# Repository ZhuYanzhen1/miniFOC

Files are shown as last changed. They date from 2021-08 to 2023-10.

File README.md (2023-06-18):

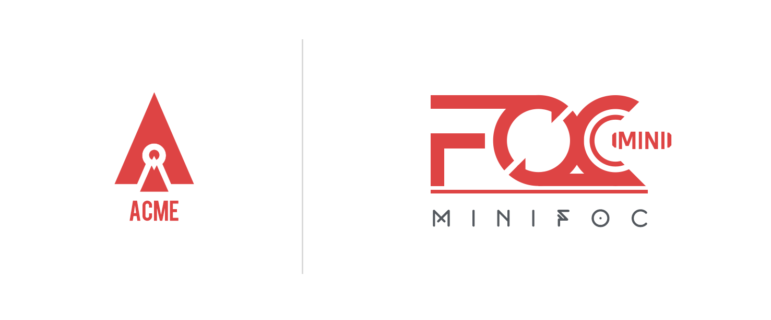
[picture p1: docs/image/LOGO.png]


&nbsp;&nbsp;&nbsp;&nbsp;&nbsp;&nbsp;&nbsp;&nbsp;&nbsp;&nbsp;&nbsp;&nbsp;&nbsp;&nbsp;&nbsp;&nbsp;English / [中文](https://github.com/ZhuYanzhen1/miniFOC/blob/main/README_CN.md)

&nbsp;&nbsp;&nbsp;&nbsp;Are you still buying a DC brush motor drive module in about 3<span>$</span>? Are you still worried about the high noise in addition to the already low response speed and life? Allow me to present you our project, miniFOC---- a FOC brushless motor control scheme that can get you the most bang for your buck, for just 3 <span>$</span>!  **miniFOC** has a built-in torque closed-loop controller so that you can control a brushless motor with a 3-wire UART port. The software and hardware design are fully compliant with the AGPL-3.0 open source license.

**Note: miniFOC V2 version is under development(dev branch) to support current loop and sensorless FOC algorithm, please look forward to it.**

***

### Brief Introduction

&nbsp;&nbsp;&nbsp;&nbsp;This open-source project aims to accomplish a FOC(Field Oriented Control) scheme that is operatable with minimum costs in China. The components selected in the example circuit are all manufactured in China. FOC possesses various advantages when it comes to controlling BLCD (Brushless Direct Current) motor; some of the benefits are as follows:

1. FOC has no speed limit at all and can be accurately controlled at any speed
2. FOC excels at its reversing performance, ensuring the smoothness of forward and reverse switching even when running at its highest speed
3. FOC can also perform braking control in the form of energy recovery.
4. FOC can achieve three closed-loop control of torque, speed, and position.
5. FOC has significantly lower noise but much higher efficiency compared that of electric regulation

&nbsp;&nbsp;&nbsp;Although FOC has many advantages, its large amount of calculation and complex principles requires an expensive controller, which made FOC unpopular. After half a year’s research and iteration, I deeply optimized the part of the code that implements mass calculations and re-selected its components to fit the domestic supply chain. I hope this open-source project can help domestic developers use BLDC motors with excellent performance and contribute to the open-source community.

***

### Comparison Of Open Source Solutions

| Open source solution | **miniFOC** | [simpleFOC](https://github.com/simplefoc/Arduino-SimpleFOCShield) | [ODrive](https://github.com/odriverobotics/ODrive) | [FpOC](https://github.com/WangXuan95/FpOC) |
| :---: | :---: | :---: | :---: | :---: |
| Microcontroller | GD32F130G6U6 | ATmega328P | STM32F405RGT6 | FPGA |
| Driver chip | EG2133 | L6234 | DRV8301 | MP6540 |
| PID loop frequency | 30kHz (max) | 830Hz (max) | 8kHz (typical) | 18kHz (typical) |
| Whether have current loop | No | No | Yes | Yes |
| Driving power | 90W | 120W | 960W | 90W |
| Cost price (approx.) | 20¥ | 100¥ | 300¥ | 150¥ |

&nbsp;&nbsp;&nbsp;&nbsp;As can be seen from the table above, the scheme adopted by **miniFOC** can achieve high performance at low cost. At the same time, due to the re-selection according to the domestic supply chain, the selection of devices is not so limited, and there are many alternatives. amid the chip shortage in 2021, the cost of FOC still can be controlled at about 3$, which further proves the degree of cost optimization and the great potential of the project.

***

### Performance Parameter 

+ Input voltage range: 5V ~ 18V (you can modify the circuit according to the tutorial here to adapt to higher voltage).
+ Maximum driving current: 5A (you can modify the circuit according to the tutorial here to achieve greater driving current).
+ Detailed parameters of FOC: no current loop control, SVPWM (Space Vector Pulse Width Modulation) is adopted.
+ Communication parameters: UART baud rate is 115200, and [Mid Capacity Data Transmit Protocol](https://github.com/ZhuYanzhen1/CDTP/blob/master/mdtp/README.md) is used for data transmission.
+ Microcontroller parameters: Cortex-M3 core, 72MHz frequency, 32KB FLASH, 4KB SRAM. 

***

### Function Features

+ [x] Using space vector pulse width modulation
+ [x] Torque control without current sensor
+ [x] Rotational speed closed loop control
+ [x] Rotation angle closed loop control
+ [x] Automatic phase sequence detection and correction

***

### Development Environment 

+ EDA Tool: [EasyEDA](https://easyeda.com/) (the standard free license is adopted, and there is no license dispute).
+ Compiler tool chain: gcc-arm-none-eabi 10-2020-q4-major
+ Programming tool: OpenOCD 0.11.0-1
+ Integrated development tools: CLion 2021.2.3 #212.5457.51
+ Software development tools: Qt 5.14.2 (MinGW 7.3.0 64bit)
+ Operating system and tool chain: 
  + Win10 + MinGW + CLion + gcc-arm-none-eabi + OpenOCD
  + Ubuntu20.04 + make + cmake + gcc-arm-none-eabi + OpenOCD

***

### Getting Started

Please refer to the [wiki page](https://github.com/ZhuYanzhen1/miniFOC/wiki) of this project for getting started.
<br>
We also provide the [domestic image](https://gitee.com/zhuyanzhen1/mini-foc) address.
<br>
You can visit [Github Page](https://zhuyanzhen1.github.io/miniFOC/) to learn about the usage of functions and variables in the code.
<br>
**Note:** Since the main development and deployment are carried out on Github, Gitee is only used as a domestic mirror warehouse to store the code, and there will be problems such as wiki and issue that are not updated in time. You can visit the Github source repository [here](https://github.com/ZhuYanzhen1/miniFOC).

***

### Bugs & Feature Requests

Please report bugs and request features using the [Issue Tracker](https://github.com/ZhuYanzhen1/miniFOC/issues) and follow these request:

1. Tab highlight when on different tab.
2. Don’t let the update disappear if the window is not in focus.

***

### License

The source code is released under a [AGPL-3.0 License](https://github.com/ZhuYanzhen1/miniFOC/blob/main/LICENSE).

**Affiliation：AcmeTech<br>
Author: Zhu Yanzhen<br>
Maintainer：YanzhenZhu, 2208213223@qq.com**

&nbsp;&nbsp;&nbsp;&nbsp;The product has been tested under Windows 10 and Ubuntu 18.04 and 20.04. This is research code, expect that it changes often and any fitness for a particular purpose is disclaimed.

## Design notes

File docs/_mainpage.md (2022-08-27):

### Function manual / 函数手册
### Introduction / 简介

&nbsp;&nbsp;&nbsp;&nbsp;This GitHub page is automatically generated by Doxygen according to code comments. It describes the purpose, function and usage of functions, variables and structures in each file except the library functions provided by gd32. You can click the "file - > file list" button at the top of the page to jump to the file list to view the description of the variables and functions declared in the relevant files.

&nbsp;&nbsp;&nbsp;&nbsp;本Github Page由Doxygen根据代码注释自动生成，描述了除了GD32提供的库函数外的每个文件中函数、变量与结构体的用途、功能和用法。你可以通过点击页面上方的“File -> File List”按钮跳转到文件列表以查看相关文件内部声明的变量和函数的说明。

### Download and  Description / 下载与描述

&nbsp;&nbsp;&nbsp;&nbsp;The content published below is the. Hex firmware generated by GitHub action scheduled task every time. The purpose is to automatically compile and publish the latest committed firmware under the main branch without manual compilation by the developer. It should be noted that the. Hex firmware on this page does not guarantee its stability and availability. If you want to download stable and available firmware, please go to the [Release Page](https://github.com/ZhuYanzhen1/miniFOC/releases) to download it.

&nbsp;&nbsp;&nbsp;&nbsp;下面发布的内容是每次由Github Action定时任务生成的.hex固件，目的是自动编译发布main分支下最新commit的固件而无需开发者手动编译。需要注意的是，本页面下的.hex固件不保证它的稳定性和可用性。如果你想下载稳定可用的固件，请转到[Release页面](https://github.com/ZhuYanzhen1/miniFOC/releases)下载。&nbsp;
 
+ [20220827](https://raw.githubusercontent.com/ZhuYanzhen1/miniFOC_Firmware/master/202208/20220827.hex): 5edd0af Merge branch 'main' of github.com:ZhuYanzhen1/miniFOC
 
+ [20220802](https://raw.githubusercontent.com/ZhuYanzhen1/miniFOC_Firmware/master/202208/20220802.hex): 6951035 Update Doxygen documentation

+ [20220801](https://raw.githubusercontent.com/ZhuYanzhen1/miniFOC_Firmware/master/202208/20220801.hex): abed215 Add SVPWM modulation code, which can be controlled by using macros.

+ [20220524](https://raw.githubusercontent.com/ZhuYanzhen1/miniFOC_Firmware/master/202205/20220524.hex): dd0dbc8 Update cmake.yml

+ [20211108](https://raw.githubusercontent.com/ZhuYanzhen1/miniFOC_Firmware/master/202111/20211108.hex): df8533c Change the automatic compilation workflow to run only when the push event occurs.

+ [20211107](https://raw.githubusercontent.com/ZhuYanzhen1/miniFOC_Firmware/master/202111/20211107.hex): bb8409a Update new firmware link to Github Pages

+ [20211106](https://raw.githubusercontent.com/ZhuYanzhen1/miniFOC_Firmware/master/202111/20211106.hex): 62c17af Merge branch 'main' of github.com:ZhuYanzhen1/miniFOC into main

+ [20211105](https://raw.githubusercontent.com/ZhuYanzhen1/miniFOC_Firmware/master/202111/20211105.hex): 08164bb Merge remote-tracking branch 'origin/main' into main

+ [20211104](https://raw.githubusercontent.com/ZhuYanzhen1/miniFOC_Firmware/master/202111/20211104.hex): 6a5dcd3 Added the button and method of flash writing content control. There are still problems with parameter reading and slider display that need to be modified.

+ [20211103](https://raw.githubusercontent.com/ZhuYanzhen1/miniFOC_Firmware/master/202111/20211103.hex): ef97f44 Update new firmware link to Github Pages

+ [20211102](https://raw.githubusercontent.com/ZhuYanzhen1/miniFOC_Firmware/master/202111/20211102.hex): b5687f6 Update new firmware link to Github Pages

+ [20211101](https://raw.githubusercontent.com/ZhuYanzhen1/miniFOC_Firmware/master/202111/20211101.hex): c459ea9 Update new firmware link to Github Pages

+ [20211031](https://raw.githubusercontent.com/ZhuYanzhen1/miniFOC_Firmware/master/202110/20211031.hex): 8e82bd1 Merge branch 'main' of github.com:ZhuYanzhen1/miniFOC into main

+ [20211030](https://raw.githubusercontent.com/ZhuYanzhen1/miniFOC_Firmware/master/202110/20211030.hex): 8c464a0 Delete a piece of wire floating in the PCB. Generate and update coordinate files and Gerber files.

+ [20211029](https://raw.githubusercontent.com/ZhuYanzhen1/miniFOC_Firmware/master/202110/20211029.hex): c5ee9a1 Merge branch 'main' of github.com:ZhuYanzhen1/miniFOC into main

+ [20211020](https://raw.githubusercontent.com/ZhuYanzhen1/miniFOC_Firmware/master/202110/20211020.hex): e1f4f51 Modify the GitHub action timed automatic compilation firmware to compile only when push occurs.

+ [20211012](https://raw.githubusercontent.com/ZhuYanzhen1/miniFOC_Firmware/master/202110/20211012.hex): 5aa44fc Merge remote-tracking branch 'origin/main' into main

+ [20211011](https://raw.githubusercontent.com/ZhuYanzhen1/miniFOC_Firmware/master/202110/20211011.hex): 22d07b8 add two lables in monitor

+ [20211010](https://raw.githubusercontent.com/ZhuYanzhen1/miniFOC_Firmware/master/202110/20211010.hex): 7520c1e Modify the main page of Doxygen generated documents to readme file as the main page.

+ [20211009](https://raw.githubusercontent.com/ZhuYanzhen1/miniFOC_Firmware/master/202110/20211009.hex): 1fdb661 Modify most of the files in the algorithm folder to a format recognized by Doxygen.

+ [20211008](https://raw.githubusercontent.com/ZhuYanzhen1/miniFOC_Firmware/master/202110/20211008.hex): 96d4344 Update new firmware link to Github Pages

+ [20211007](https://raw.githubusercontent.com/ZhuYanzhen1/miniFOC_Firmware/master/202110/20211007.hex): e1db21f Update new firmware link to Github Pages

+ [20211006](https://raw.githubusercontent.com/ZhuYanzhen1/miniFOC_Firmware/master/202110/20211006.hex): 8ff27a8 Update new firmware link to Github Pages

+ [20211005](https://raw.githubusercontent.com/ZhuYanzhen1/miniFOC_Firmware/master/202110/20211005.hex): 9e18ca4 Update new firmware link to Github Pages

+ [20211004](https://raw.githubusercontent.com/ZhuYanzhen1/miniFOC_Firmware/master/202110/20211004.hex): 9ad907a Correct the medium capacity data transfer protocol link in README.

+ [20210930](https://raw.githubusercontent.com/ZhuYanzhen1/miniFOC_Firmware/master/202109/20210930.hex): 62079a2 Merge branch 'main' of github.com:ZhuYanzhen1/miniFOC into main

+ [20210929](https://raw.githubusercontent.com/ZhuYanzhen1/miniFOC_Firmware/master/202109/20210929.hex): 0ad9f00 Add comments for PID program.

+ [20210928](https://raw.githubusercontent.com/ZhuYanzhen1/miniFOC_Firmware/master/202109/20210928.hex): 6c3f43f Update new firmware link to Github Pages

+ [20210927](https://raw.githubusercontent.com/ZhuYanzhen1/miniFOC_Firmware/master/202109/20210927.hex): 4ef3bf9 Update new firmware link to Github Pages

+ [20210926](https://raw.githubusercontent.com/ZhuYanzhen1/miniFOC_Firmware/master/202109/20210926.hex): 13c4a77 Add the slider position and the maximum and minimum value change code for the monitor. Now the parameters of the motor can be parsed and reflected on the slider.

+ [20210925](https://raw.githubusercontent.com/ZhuYanzhen1/miniFOC_Firmware/master/202109/20210925.hex): 4c8ae1b Update new firmware link to Github Pages

+ [20210924](https://raw.githubusercontent.com/ZhuYanzhen1/miniFOC_Firmware/master/202109/20210924.hex): 00c7781 The problem of sending messages after the monitor is started has been solved. The problem of enabling logic of slider control in monitor is solved.

+ [20210923](https://raw.githubusercontent.com/ZhuYanzhen1/miniFOC_Firmware/master/202109/20210923.hex): bfeb755 Add the variable return function to sort out the uploaded functions into the report. C file.

+ [20210922](https://raw.githubusercontent.com/ZhuYanzhen1/miniFOC_Firmware/master/202109/20210922.hex): f3c4b4f Modify the development environment version in readme and add notes for the image repo.

+ [20210921](https://raw.githubusercontent.com/ZhuYanzhen1/miniFOC_Firmware/master/202109/20210921.hex): 5607792 Merge branch 'main' of github.com:ZhuYanzhen1/miniFOC into main

+ [20210920](https://raw.githubusercontent.com/ZhuYanzhen1/miniFOC_Firmware/master/202109/20210920.hex): 06330fe Correct the FOC twice coordinate transformation annotation.

+ [20210919](https://raw.githubusercontent.com/ZhuYanzhen1/miniFOC_Firmware/master/202109/20210919.hex): 626c4fb Modify the global variable name so that it does not duplicate.

+ [20210918](https://raw.githubusercontent.com/ZhuYanzhen1/miniFOC_Firmware/master/202109/20210918.hex): 35eb651 Modify README and update mainwindow.ui of monitor

+ [20210917](https://raw.githubusercontent.com/ZhuYanzhen1/miniFOC_Firmware/master/202109/20210917.hex): b5a9140 Update new firmware link to Github Pages

+ [20210916](https://raw.githubusercontent.com/ZhuYanzhen1/miniFOC_Firmware/master/202109/20210916.hex): 813b97e Add speed update configure macro to config.h.

+ [20210914](https://raw.githubusercontent.com/ZhuYanzhen1/miniFOC_Firmware/master/202109/20210914.hex): 975d112 Update new firmware link to Github Pages

+ [20210913](https://raw.githubusercontent.com/ZhuYanzhen1/miniFOC_Firmware/master/202109/20210913.hex): 3207bc9 The PCB circuit of minifoc is modified

+ [20210912](https://raw.githubusercontent.com/ZhuYanzhen1/miniFOC_Firmware/master/202109/20210912.hex): 43bdf80 Fixed the problem that the reverse speed could not be measured during speed calculation.

+ [20210911](https://raw.githubusercontent.com/ZhuYanzhen1/miniFOC_Firmware/master/202109/20210911.hex): 610eeb6 Add a comment for timer deactivation.

+ [20210910](https://raw.githubusercontent.com/ZhuYanzhen1/miniFOC_Firmware/master/202109/20210910.hex): 97ade83 Modify the packet serial port sending function, and now you can send data correctly.

+ [20210909](https://raw.githubusercontent.com/ZhuYanzhen1/miniFOC_Firmware/master/202109/20210909.hex): 9216fd7 Add upper computer monitor tools for miniFOC

+ [20210908](https://raw.githubusercontent.com/ZhuYanzhen1/miniFOC_Firmware/master/202109/20210908.hex): 0eef12c Normalize variable names and adjust the order.

+ [20210907](https://raw.githubusercontent.com/ZhuYanzhen1/miniFOC_Firmware/master/202109/20210907.hex): 238b89d Fix mdtp_callback_handler function name mismatch.

+ [20210906](https://raw.githubusercontent.com/ZhuYanzhen1/miniFOC_Firmware/master/202109/20210906.hex): 791bb85 Normalized FLASH read / write function name.

+ [20210905](https://raw.githubusercontent.com/ZhuYanzhen1/miniFOC_Firmware/master/202109/20210905.hex): be1d8fa The speed calculation code and sliding window filter function are added to make the speed smoother.

+ [20210904](https://raw.githubusercontent.com/ZhuYanzhen1/miniFOC_Firmware/master/202109/20210904.hex): 84aa5d8 Polish README

+ [20210903](https://raw.githubusercontent.com/ZhuYanzhen1/miniFOC_Firmware/master/202109/20210903.hex): ebb2498 The electric angle correction program is added. The pole number and encoder resolution are added to the config file for modification. Corrected PWM initialization duty cycle to prevent power on burn out.

+ [20210902](https://raw.githubusercontent.com/ZhuYanzhen1/miniFOC_Firmware/master/202109/20210902.hex): 21ed3dd Add read and initialization functions of magnetic encoder. Add comments for SPI related functions and move SPI frequency division coefficient to config file for configuration.

+ [20210901](https://raw.githubusercontent.com/ZhuYanzhen1/miniFOC_Firmware/master/202109/20210901.hex): 2698c41 Merge branch 'main' of github.com:ZhuYanzhen1/miniFOC into main

+ [20210831](https://raw.githubusercontent.com/ZhuYanzhen1/miniFOC_Firmware/master/202108/20210831.hex): 2d309e9 Code comments are added for fast mathematical calculation functions and FOC calculation functions.

+ [20210830](https://raw.githubusercontent.com/ZhuYanzhen1/miniFOC_Firmware/master/202108/20210830.hex): 021d7fa The fast mathematical calculation function is added to accelerate the calculation speed of sin and cos calculate, and the program volume is reduced (compared with using math Standard Library).

+ [20210829](https://raw.githubusercontent.com/ZhuYanzhen1/miniFOC_Firmware/master/202108/20210829.hex): 1e40d66 Add and update PWM duty cycle function. Add comments for PWM initialization function and modify initialization channel.

+ [20210828](https://raw.githubusercontent.com/ZhuYanzhen1/miniFOC_Firmware/master/202108/20210828.hex): 0a068b2 Add wiki repo into docs directory

+ [20210827](https://raw.githubusercontent.com/ZhuYanzhen1/miniFOC_Firmware/master/202108/20210827.hex): 924f307 Merge branch 'main' of github.com:ZhuYanzhen1/miniFOC into main

+ [20210826](https://raw.githubusercontent.com/ZhuYanzhen1/miniFOC_Firmware/master/202108/20210826.hex): dfea67b Add the packet function of medium capacity transmission protocol. When the data packet is received, it is sent back according to the original packet to test whether the function of receiving and sending data packet can operate normally.

+ [20210825](https://raw.githubusercontent.com/ZhuYanzhen1/miniFOC_Firmware/master/202108/20210825.hex): 0e68071 Some data receiving functions are realized. Annotate the functions in the system file. Fixed missing systick handler. The memset function is rewritten, and the program volume can be reduced without using the standard library.

+ [20210824](https://raw.githubusercontent.com/ZhuYanzhen1/miniFOC_Firmware/master/202108/20210824.hex): 1b1fd54 Add UART0 initialization code, file author declaration, function declaration and code comments. Add config header file to facilitate users to modify important parameters.

+ [20210823](https://raw.githubusercontent.com/ZhuYanzhen1/miniFOC_Firmware/master/202108/20210823.hex): c774ad1 Add macro definition of LED level toggle.

+ [20210822](https://raw.githubusercontent.com/ZhuYanzhen1/miniFOC_Firmware/master/202108/20210822.hex): c625232 Delete testing files

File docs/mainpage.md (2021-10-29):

### Function manual / 函数手册
### Introduction / 简介

&nbsp;&nbsp;&nbsp;&nbsp;This GitHub page is automatically generated by Doxygen according to code comments. It describes the purpose, function and usage of functions, variables and structures in each file except the library functions provided by gd32. You can click the "file - > file list" button at the top of the page to jump to the file list to view the description of the variables and functions declared in the relevant files.

&nbsp;&nbsp;&nbsp;&nbsp;本Github Page由Doxygen根据代码注释自动生成，描述了除了GD32提供的库函数外的每个文件中函数、变量与结构体的用途、功能和用法。你可以通过点击页面上方的“File -> File List”按钮跳转到文件列表以查看相关文件内部声明的变量和函数的说明。

### Download and  Description / 下载与描述

&nbsp;&nbsp;&nbsp;&nbsp;The content published below is the. Hex firmware generated by GitHub action scheduled task every time. The purpose is to automatically compile and publish the latest committed firmware under the main branch without manual compilation by the developer. It should be noted that the. Hex firmware on this page does not guarantee its stability and availability. If you want to download stable and available firmware, please go to the [Release Page](https://github.com/ZhuYanzhen1/miniFOC/releases) to download it.

&nbsp;&nbsp;&nbsp;&nbsp;下面发布的内容是每次由Github Action定时任务生成的.hex固件，目的是自动编译发布main分支下最新commit的固件而无需开发者手动编译。需要注意的是，本页面下的.hex固件不保证它的稳定性和可用性。如果你想下载稳定可用的固件，请转到[Release页面](https://github.com/ZhuYanzhen1/miniFOC/releases)下载。&nbsp;

+ [20211029](https://gitee.com/zhuyanzhen1/minifoc_firmware/raw/master/202110/20211029.hex): 1254535 Merge remote-tracking branch 'origin/main' into main
 
+ [20211020](https://gitee.com/zhuyanzhen1/minifoc_firmware/raw/master/202110/20211020.hex): e1f4f51 Modify the GitHub action timed automatic compilation firmware to compile only when push occurs.
>>>>>>> beb967e1ab6f77c084e02630ea8d8368526810f3:docs/index.md

+ [20211012](https://gitee.com/zhuyanzhen1/minifoc_firmware/raw/master/202110/20211012.hex): 5aa44fc Merge remote-tracking branch 'origin/main' into main

+ [20211011](https://gitee.com/zhuyanzhen1/minifoc_firmware/raw/master/202110/20211011.hex): 22d07b8 add two lables in monitor

+ [20211010](https://gitee.com/zhuyanzhen1/minifoc_firmware/raw/master/202110/20211010.hex): 7520c1e Modify the main page of Doxygen generated documents to readme file as the main page.

+ [20211009](https://gitee.com/zhuyanzhen1/minifoc_firmware/raw/master/202110/20211009.hex): 1fdb661 Modify most of the files in the algorithm folder to a format recognized by Doxygen.

+ [20211008](https://gitee.com/zhuyanzhen1/minifoc_firmware/raw/master/202110/20211008.hex): 96d4344 Update new firmware link to Github Pages

+ [20211007](https://gitee.com/zhuyanzhen1/minifoc_firmware/raw/master/202110/20211007.hex): e1db21f Update new firmware link to Github Pages

+ [20211006](https://gitee.com/zhuyanzhen1/minifoc_firmware/raw/master/202110/20211006.hex): 8ff27a8 Update new firmware link to Github Pages

+ [20211005](https://gitee.com/zhuyanzhen1/minifoc_firmware/raw/master/202110/20211005.hex): 9e18ca4 Update new firmware link to Github Pages

+ [20211004](https://gitee.com/zhuyanzhen1/minifoc_firmware/raw/master/202110/20211004.hex): 9ad907a Correct the medium capacity data transfer protocol link in README.

+ [20210930](https://gitee.com/zhuyanzhen1/minifoc_firmware/raw/master/202109/20210930.hex): 62079a2 Merge branch 'main' of github.com:ZhuYanzhen1/miniFOC into main

+ [20210929](https://gitee.com/zhuyanzhen1/minifoc_firmware/raw/master/202109/20210929.hex): 0ad9f00 Add comments for PID program.

+ [20210928](https://gitee.com/zhuyanzhen1/minifoc_firmware/raw/master/202109/20210928.hex): 6c3f43f Update new firmware link to Github Pages

+ [20210927](https://gitee.com/zhuyanzhen1/minifoc_firmware/raw/master/202109/20210927.hex): 4ef3bf9 Update new firmware link to Github Pages

+ [20210926](https://gitee.com/zhuyanzhen1/minifoc_firmware/raw/master/202109/20210926.hex): 13c4a77 Add the slider position and the maximum and minimum value change code for the monitor. Now the parameters of the motor can be parsed and reflected on the slider.

+ [20210925](https://gitee.com/zhuyanzhen1/minifoc_firmware/raw/master/202109/20210925.hex): 4c8ae1b Update new firmware link to Github Pages

+ [20210924](https://gitee.com/zhuyanzhen1/minifoc_firmware/raw/master/202109/20210924.hex): 00c7781 The problem of sending messages after the monitor is started has been solved. The problem of enabling logic of slider control in monitor is solved.

+ [20210923](https://gitee.com/zhuyanzhen1/minifoc_firmware/raw/master/202109/20210923.hex): bfeb755 Add the variable return function to sort out the uploaded functions into the report. C file.

+ [20210922](https://gitee.com/zhuyanzhen1/minifoc_firmware/raw/master/202109/20210922.hex): f3c4b4f Modify the development environment version in readme and add notes for the image repo.

+ [20210921](https://gitee.com/zhuyanzhen1/minifoc_firmware/raw/master/202109/20210921.hex): 5607792 Merge branch 'main' of github.com:ZhuYanzhen1/miniFOC into main

+ [20210920](https://gitee.com/zhuyanzhen1/minifoc_firmware/raw/master/202109/20210920.hex): 06330fe Correct the FOC twice coordinate transformation annotation.

+ [20210919](https://gitee.com/zhuyanzhen1/minifoc_firmware/raw/master/202109/20210919.hex): 626c4fb Modify the global variable name so that it does not duplicate.

+ [20210918](https://gitee.com/zhuyanzhen1/minifoc_firmware/raw/master/202109/20210918.hex): 35eb651 Modify README and update mainwindow.ui of monitor

+ [20210917](https://gitee.com/zhuyanzhen1/minifoc_firmware/raw/master/202109/20210917.hex): b5a9140 Update new firmware link to Github Pages

+ [20210916](https://gitee.com/zhuyanzhen1/minifoc_firmware/raw/master/202109/20210916.hex): 813b97e Add speed update configure macro to config.h.

+ [20210914](https://gitee.com/zhuyanzhen1/minifoc_firmware/raw/master/202109/20210914.hex): 975d112 Update new firmware link to Github Pages

+ [20210913](https://gitee.com/zhuyanzhen1/minifoc_firmware/raw/master/202109/20210913.hex): 3207bc9 The PCB circuit of minifoc is modified

+ [20210912](https://gitee.com/zhuyanzhen1/minifoc_firmware/raw/master/202109/20210912.hex): 43bdf80 Fixed the problem that the reverse speed could not be measured during speed calculation.

+ [20210911](https://gitee.com/zhuyanzhen1/minifoc_firmware/raw/master/202109/20210911.hex): 610eeb6 Add a comment for timer deactivation.

+ [20210910](https://gitee.com/zhuyanzhen1/minifoc_firmware/raw/master/202109/20210910.hex): 97ade83 Modify the packet serial port sending function, and now you can send data correctly.

+ [20210909](https://gitee.com/zhuyanzhen1/minifoc_firmware/raw/master/202109/20210909.hex): 9216fd7 Add upper computer monitor tools for miniFOC

+ [20210908](https://gitee.com/zhuyanzhen1/minifoc_firmware/raw/master/202109/20210908.hex): 0eef12c Normalize variable names and adjust the order.

+ [20210907](https://gitee.com/zhuyanzhen1/minifoc_firmware/raw/master/202109/20210907.hex): 238b89d Fix mdtp_callback_handler function name mismatch.

+ [20210906](https://gitee.com/zhuyanzhen1/minifoc_firmware/raw/master/202109/20210906.hex): 791bb85 Normalized FLASH read / write function name.

+ [20210905](https://gitee.com/zhuyanzhen1/minifoc_firmware/raw/master/202109/20210905.hex): be1d8fa The speed calculation code and sliding window filter function are added to make the speed smoother.

+ [20210904](https://gitee.com/zhuyanzhen1/minifoc_firmware/raw/master/202109/20210904.hex): 84aa5d8 Polish README

+ [20210903](https://gitee.com/zhuyanzhen1/minifoc_firmware/raw/master/202109/20210903.hex): ebb2498 The electric angle correction program is added. The pole number and encoder resolution are added to the config file for modification. Corrected PWM initialization duty cycle to prevent power on burn out.

+ [20210902](https://gitee.com/zhuyanzhen1/minifoc_firmware/raw/master/202109/20210902.hex): 21ed3dd Add read and initialization functions of magnetic encoder. Add comments for SPI related functions and move SPI frequency division coefficient to config file for configuration.

+ [20210901](https://gitee.com/zhuyanzhen1/minifoc_firmware/raw/master/202109/20210901.hex): 2698c41 Merge branch 'main' of github.com:ZhuYanzhen1/miniFOC into main

+ [20210831](https://gitee.com/zhuyanzhen1/minifoc_firmware/raw/master/202108/20210831.hex): 2d309e9 Code comments are added for fast mathematical calculation functions and FOC calculation functions.

+ [20210830](https://gitee.com/zhuyanzhen1/minifoc_firmware/raw/master/202108/20210830.hex): 021d7fa The fast mathematical calculation function is added to accelerate the calculation speed of sin and cos calculate, and the program volume is reduced (compared with using math Standard Library).

+ [20210829](https://gitee.com/zhuyanzhen1/minifoc_firmware/raw/master/202108/20210829.hex): 1e40d66 Add and update PWM duty cycle function. Add comments for PWM initialization function and modify initialization channel.

+ [20210828](https://gitee.com/zhuyanzhen1/minifoc_firmware/raw/master/202108/20210828.hex): 0a068b2 Add wiki repo into docs directory

+ [20210827](https://gitee.com/zhuyanzhen1/minifoc_firmware/raw/master/202108/20210827.hex): 924f307 Merge branch 'main' of github.com:ZhuYanzhen1/miniFOC into main

+ [20210826](https://gitee.com/zhuyanzhen1/minifoc_firmware/raw/master/202108/20210826.hex): dfea67b Add the packet function of medium capacity transmission protocol. When the data packet is received, it is sent back according to the original packet to test whether the function of receiving and sending data packet can operate normally.

+ [20210825](https://gitee.com/zhuyanzhen1/minifoc_firmware/raw/master/202108/20210825.hex): 0e68071 Some data receiving functions are realized. Annotate the functions in the system file. Fixed missing systick handler. The memset function is rewritten, and the program volume can be reduced without using the standard library.

+ [20210824](https://gitee.com/zhuyanzhen1/minifoc_firmware/raw/master/202108/20210824.hex): 1b1fd54 Add UART0 initialization code, file author declaration, function declaration and code comments. Add config header file to facilitate users to modify important parameters.

+ [20210823](https://gitee.com/zhuyanzhen1/minifoc_firmware/raw/master/202108/20210823.hex): c774ad1 Add macro definition of LED level toggle.

+ [20210822](https://gitee.com/zhuyanzhen1/minifoc_firmware/raw/master/202108/20210822.hex): c625232 Delete testing files

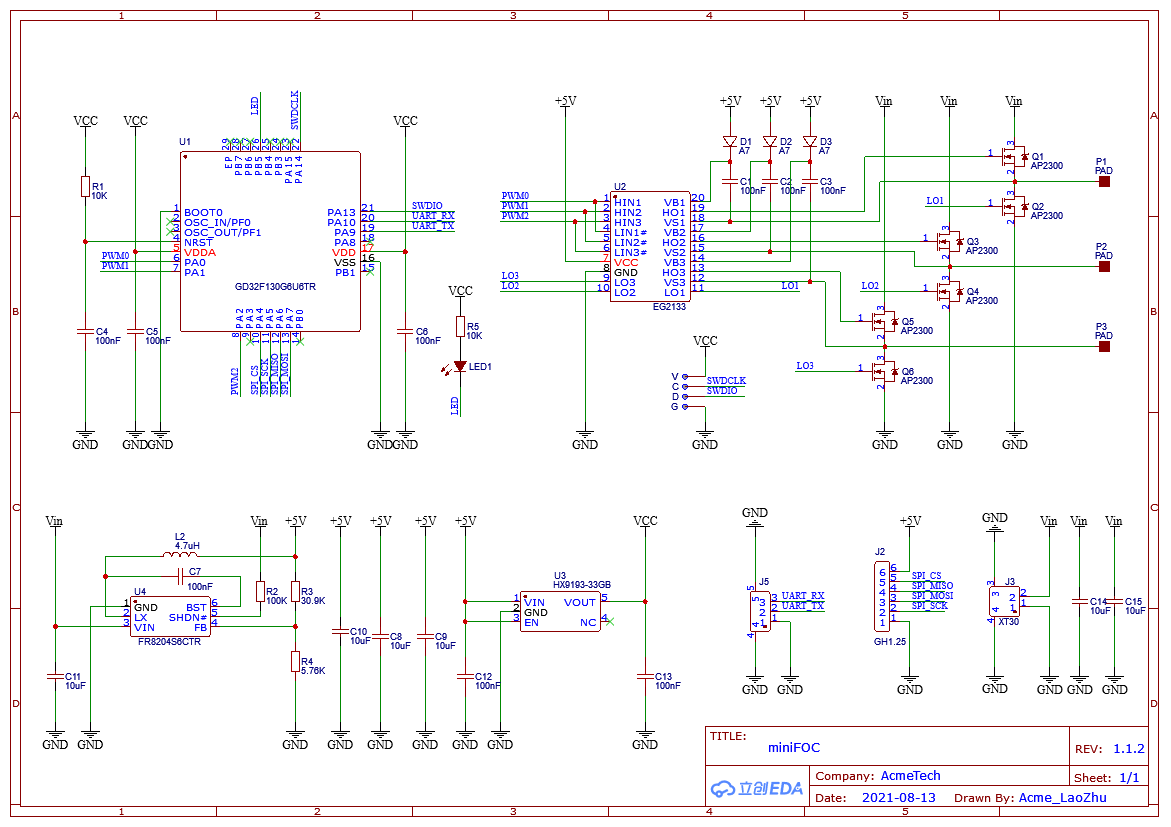
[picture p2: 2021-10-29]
docs/image/miniFOC_schematic.png

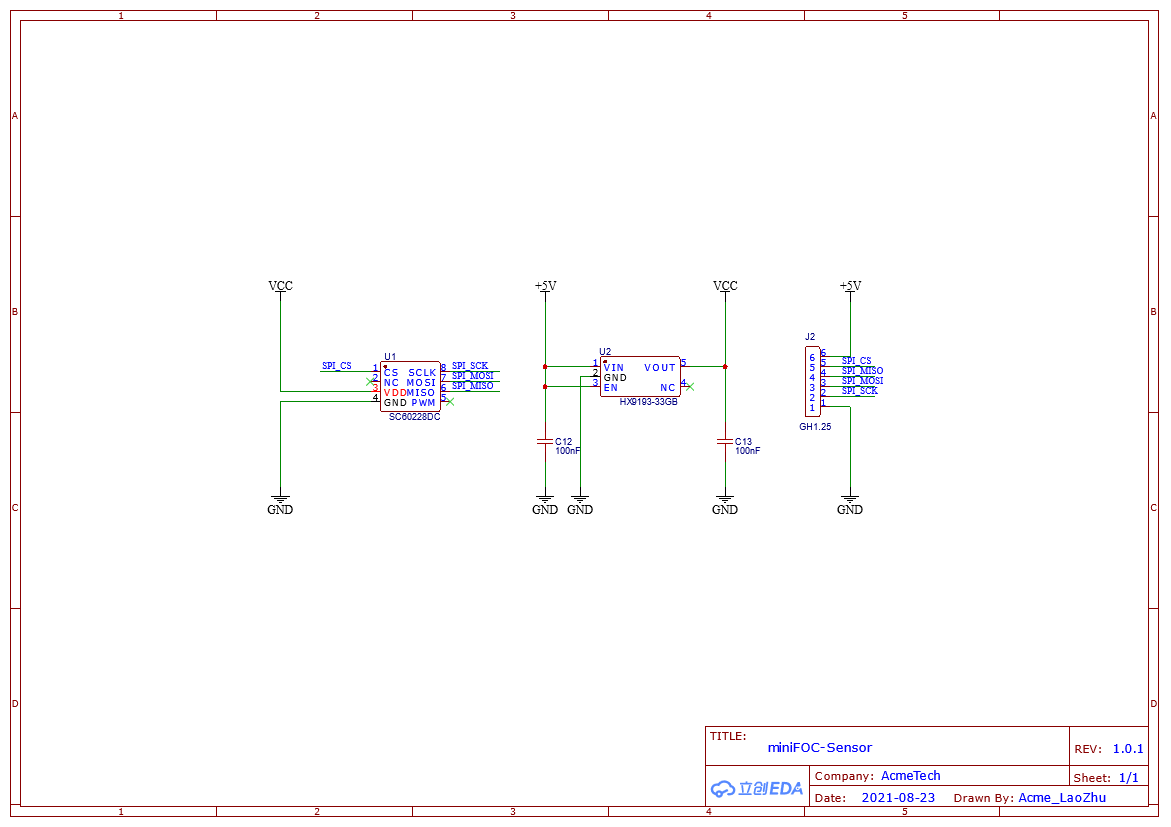
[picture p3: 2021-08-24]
docs/image/miniFOC-Sensor_schematic.png

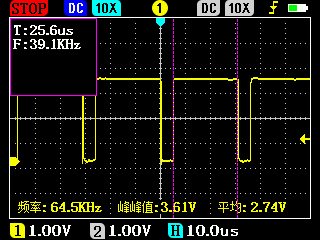
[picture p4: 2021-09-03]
docs/image/single_calculation_cycle.jpg

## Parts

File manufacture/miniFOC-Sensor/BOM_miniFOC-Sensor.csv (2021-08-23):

ID | Name | Designator | Footprint | Quantity | Manufacturer Part | Manufacturer | Supplier | Supplier Part | Price
1 | 100nF | C12,C13 | C0603 | 2 | CC0603KRX7R9BB104 | YAGEO | LCSC | C14663 | 0.0198
2 | GH1.25 | J2 | GH1.25_6P_卧贴 | 1 |  | Changjiang Connectors | LCSC | C225129 | 1.0497
3 | SC60228DC | U1 | SOIC-8_L5.0-W4.0-P1.27-LS6.0-BL | 1 | SC60228DC | Semiment | LCSC | C496752 | 12.94
4 | HX9193-33GB | U2 | SOT-23-5_L3.0-W1.7-P0.95-LS2.8-BR | 1 | HX9193-33GB | hengjiaxing | LCSC | C296123 | 0.1654

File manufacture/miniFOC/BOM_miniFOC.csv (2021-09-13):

ID | Name | Designator | Footprint | Quantity | Manufacturer Part | Manufacturer | Supplier | Supplier Part | Price
1 | 10uF | C10,C11,C14,C15 | C0805 | 4 | CL21A106KAYNNNE | SAMSUNG | LCSC | C15850 | 0.0758
2 | 100K | R2 | R0603 | 1 | 0603WAF1003T5E | UniOhm | LCSC | C25803 | 0.0067
3 | 30.9K | R3 | R0603 | 1 | RTT033092FTP | RALEC | LCSC | C103530 | 0.008
4 | 5.76K | R4 | R0603 | 1 | ARG03FTC5761 | Viking Tech | LCSC | C218094 | 0.0506
5 | FR8204S6CTR | U4 | SOT-23-6_L2.9-W1.6-P0.95-LS2.8-BR | 1 | FR8204S6CTR | FITIPOWER | LCSC | C172766 | 0.6654
6 | 100nF | C2,C3,C1,C7,C13,C4,C5,C6,C12 | C0603 | 9 | CC0603KRX7R9BB104 | YAGEO | LCSC | C14663 | 0.0159
7 | GH1.25 | J2 | GH1.25_6P_卧贴 | 1 |  | Changjiang Connectors | LCSC | C225129 | 1.2059
8 | EG2133 | U2 | TSSOP-20_L6.5-W4.4-P0.65-LS6.4-BL | 1 | EG2133 | EG Micro | LCSC | C190343 | 1.95
9 | GH1.25-3PWBPZ | J5 | CONN-SMD_GH1.25-3PWBPZ | 1 | GH1.25-3PWBPZ | BOOMELE(博穆精密) | LCSC | C2829252 | 0.3221
10 | 4.7uH | L2 | IND-SMD_L4.4-W4.0_PHC0420 | 1 | PHC0420-4R7M-T | EMTEK | LCSC | C251690 | 1.9061
11 | 19-217/BHC-ZL1M2RY/3T | LED1 | LED0603-R-RD | 1 | 19-217/BHC-ZL1M2RY/3T | EVERLIGHT | LCSC | C72041 | 0.0982
12 | 10K | R5,R1 | R0603 | 2 | 0603WAF1002T5E | UniOhm | LCSC | C25804 | 0.0066
13 | 10uF | C8,C9 | C0603 | 2 | CL10A106KP8NNNC | SAMSUNG | LCSC | C19702 | 0.0501
14 | A7 | D1,D2,D3 | SOD-123FL_L2.7-W1.8-LS3.8-RD | 3 | A7 | ZRE | LCSC | C779601 | 0.0417
15 | XT30 | J3 | CONN-TH_XT30PW-M | 1 | XT30PW-M | Changzhou Amass Elec | LCSC | C431092 | 3.88
16 | AP2300 | Q1,Q2,Q3,Q4,Q5,Q6 | SOT-23-3_L3.0-W1.7-P0.95-LS2.9-BR | 6 | AP2300 | ShenZhen Quan Li Semiconductor | LCSC | C360338 | 0.1441
17 | HX9193-33GB | U3 | SOT-23-5_L3.0-W1.7-P0.95-LS2.8-BR | 1 | HX9193-33GB | hengjiaxing | LCSC | C296123 | 0.1654
18 | GD32F130G6U6TR | U1 | QFN-28_L4.0-W4.0-P0.40-BL-EP | 1 | GD32F130G6U6TR | GigaDevice | LCSC | C94320 | 5.01

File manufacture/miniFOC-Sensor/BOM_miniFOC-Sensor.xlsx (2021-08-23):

编号 | 型号 | 封装 | 数量 | 立创编号 | 单价
C12,C13 | 100nF | C0603 | 2 | C14663 | 0.0198
J2 | GH1.25 | GH1.25_6P_卧贴 | 1 | C225129 | 1.0497
U1 | SC60228DC | SOIC-8 | 1 | C496752 | 12.94
U2 | HX9193-33GB | SOT-23-5 | 1 | C296123 | 0.1654

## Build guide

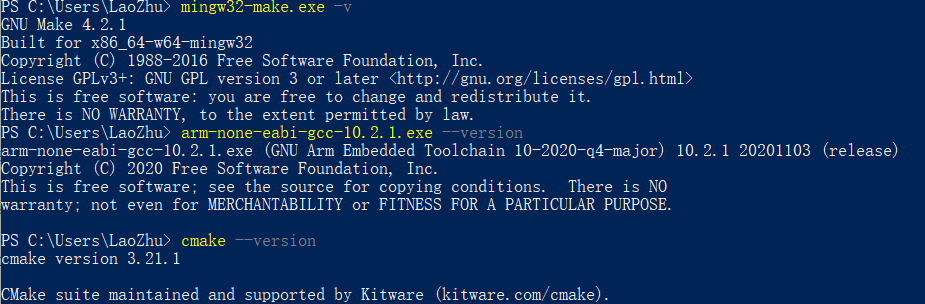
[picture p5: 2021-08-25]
docs/image/windows_check_install.png

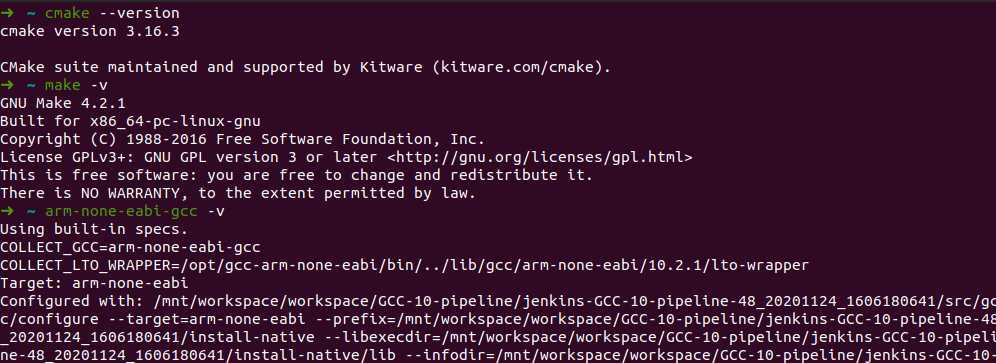
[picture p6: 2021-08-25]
docs/image/ubuntu_check_install.png

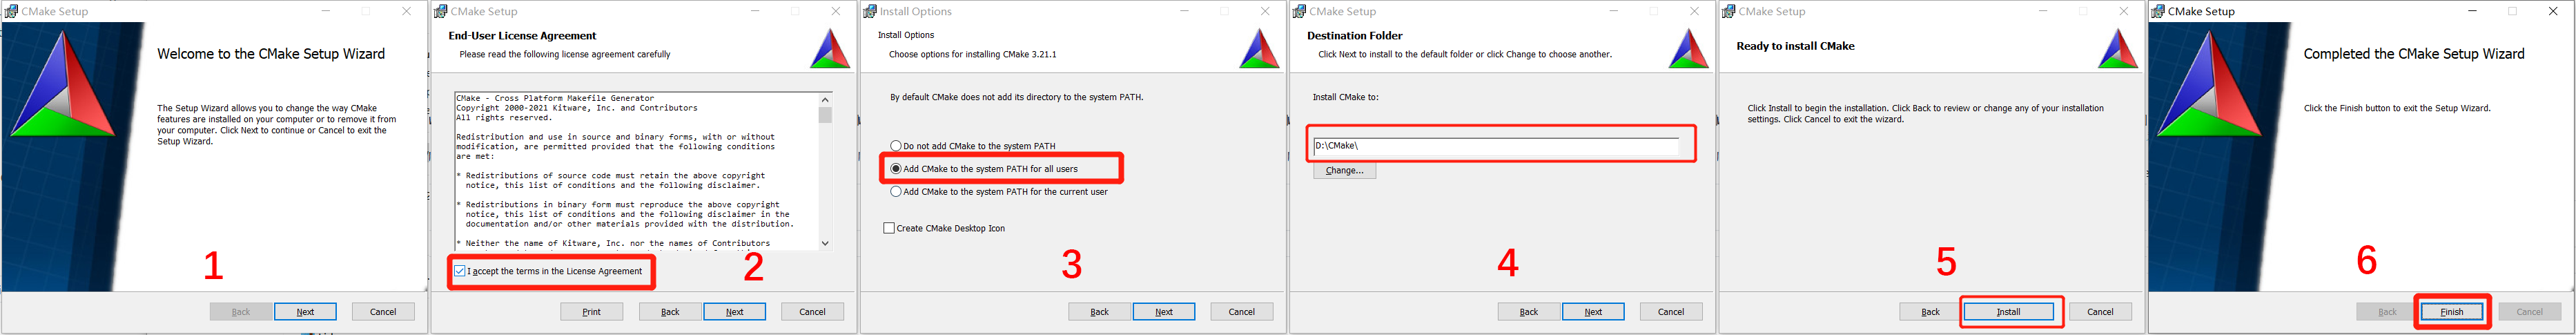
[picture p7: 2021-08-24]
docs/image/cmake_install.png

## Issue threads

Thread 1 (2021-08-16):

挺期待的！

Whitolf, 2021-08-16:
期待大佬更新！另外有几个问题：1.驱动电流是不是可以通过更换mos管获得更大的电流？2.Simplefoc好像支持了foc电流模式？

ZhuYanzhen1, 2021-08-17:
>
>
> 期待大佬更新！另外有几个问题：1.驱动电流是不是可以通过更换mos管获得更大的电流？2.Simplefoc好像支持了foc电流模式？

感谢关注！对于你的问题：
1. 可以通过更换MOS管获得更大的电流，请关注后续更新的教程
2. simpleFOC有支持电流环的branch，但是尚不十分稳定。在我移植该branch时发现效果并不理想。
3. 持续关注本项目，在未来有加入电流环的计划。

Closed 2021-08-19.

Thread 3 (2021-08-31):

[Feature] 无感FOC

asanghehe, 2021-08-31:
### Verify steps

- [X]  我已经在 [Issue Tracker](……/) 中找过我要提出的请求<br> I have searched on the [issue tracker](……/) for a related feature request.
- [X]  我已经仔细看过 [Documentation](https://github.com/ZhuYanzhen1/miniFOC/wiki) 并无法自行解决问题 I have read the [documentation](https://github.com/ZhuYanzhen1/miniFOC/wiki) and was unable to solve the issue.

### Description

这个项目目前只是有感FOC的实现吧，有计划做无感的吗

### Possible Solution

_No response_

ZhuYanzhen1, 2021-08-31:
此项目目前只是有感FOC，对于无感FOC而言这颗控制器无法提供足够的算力进行观测器部分有关的计算。如果你有加速运算的思路或者有关算法能够提供，请提交PR参与我们的开发。

asanghehe, 2021-09-17:
>
>
> 此项目目前只是有感FOC，对于无感FOC而言这颗控制器无法提供足够的算力进行观测器部分有关的计算。如果你有加速运算的思路或者有关算法能够提供，请提交PR参与我们的开发。

我看了电路图，不知道那个传感器是怎么个安装方式，能否上传个真机照片看看呢

ZhuYanzhen1, 2021-09-17:
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

传感器电路的安装上的图片如下：
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
后期我们会在wiki上补充更清晰详细的安装说明，预计九月底wiki页面会基本补全。

Closed 2021-09-02.

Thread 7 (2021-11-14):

[Feature] 是否可能移植到 esp32 的Arduino平台？

ifengchao, 2021-11-14:
### Verify steps

- [X]  我已经在 [Issue Tracker](……/) 中找过我要提出的请求<br> I have searched on the [issue tracker](……/) for a related feature request.
- [X]  我已经仔细看过 [Documentation](https://github.com/ZhuYanzhen1/miniFOC/wiki) 并无法自行解决问题 I have read the [documentation](https://github.com/ZhuYanzhen1/miniFOC/wiki) and was unable to solve the issue.

### Description

能放出开源代码，已经很了不起了！非常感谢！

### Possible Solution

如果可以支持ESP32的Arduino平台开发，相信更容易推荐开源软件的传播。
而且ESP32似乎在性能和功能上比GD32更有优势，更容易拓展。单价也很低。

ZhuYanzhen1, 2021-11-14:
> 如果可以支持ESP32的Arduino平台开发，相信更容易推荐开源软件的传播。 而且ESP32似乎在性能和功能上比GD32更有优势，更容易拓展。单价也很低。

ESP32的性能确实强于我选的这款GD32，不过它在小型化和成本上还没有压倒性的优势。这个想法很好，我之前也有想过是否要支持Arduino，无奈学业繁忙没有精力再做移植和适配。如果你有想法和能力的话可以提交pull request或者创建一个新branch进行开发。

ifengchao, 2021-11-14:
> > 如果可以支持ESP32的Arduino平台开发，相信更容易推荐开源软件的传播。 而且ESP32似乎在性能和功能上比GD32更有优势，更容易拓展。单价也很低。
>
> ESP32的性能确实强于我选的这款GD32，不过它在小型化和成本上还没有压倒性的优势。这个想法很好，我之前也有想过是否要支持Arduino，无奈学业繁忙没有精力再做移植和适配。如果你有想法和能力的话可以提交pull request或者创建一个新branch进行开发。

有时间我也会试着尝试，如果我能全部理解你的代码。

ifengchao, 2021-11-14:
http://simplefoc.cn/#/simplefoc_translation/3.7%E6%8A%80%E6%9C%AF%E8%B7%AF%E7%BA%BF
刚刚看到灯哥开源介绍的simplefoc路线，他们对ESP32做了支持，关注的伙伴可以了解下。

microcai, 2023-11-25:
ESP32 有 freertos 和 ardunio 两种平台。建议直接用 freertos 的。ardunio 平台封装的非常臃肿，加个电机库后， flash 就快吃完了。没法加 wifi 了。

Closed 2021-11-14.

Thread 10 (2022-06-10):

[Feature] 支持 无感 吗?

mikewen, 2022-06-10:
### Verify steps

- [X]  我已经在 [Issue Tracker](……/) 中找过我要提出的请求<br> I have searched on the [issue tracker](……/) for a related feature request.
- [X]  我已经仔细看过 [Documentation](https://github.com/ZhuYanzhen1/miniFOC/wiki) 并无法自行解决问题 I have read the [documentation](https://github.com/ZhuYanzhen1/miniFOC/wiki) and was unable to solve the issue.

### Description

有没有可能支持无感? sensorless FOC

### Possible Solution

_No response_

ZhuYanzhen1, 2022-06-12:
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

目前还不支持无感，后续可以考虑增加这个feature。原因是无感并不适合低速场景，而本miniFOC项目主要是为低速如关节电机场景设计的。

ZhuYanzhen1, 2023-10-14:
miniFOC v2.0.2版本即将支持无感，请关注dev分支。

ZhuYanzhen1, 2023-12-11:
> 在这种低速的场合，无感的成本反而会更高。虽然违反直觉，但是这就是试试。无感方案需要添加3个电流采用放大器。还需要升级 mcu 要有足够的算力。 这些升级的成本反而远超一个编码器的成本。

不一定。低速可以用高频注入的方法实现，可以在不增加任何电路的情况下做到低速无感。同时MCU算力其实并不需要非常高。就miniFOC v2使用的CH32V203这颗MCU而言，做了定点计算优化之后的算法做一次闭环的计算耗时在4us左右，绰绰有余了。

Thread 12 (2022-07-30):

[Feature] FOC调制算法似乎不是SVPWM？

HangX-Ma, 2022-07-30:
### Verify steps

- [X]  我已经在 [Issue Tracker](……/) 中找过我要提出的请求<br> I have searched on the [issue tracker](……/) for a related feature request.
- [X]  我已经仔细看过 [Documentation](https://github.com/ZhuYanzhen1/miniFOC/wiki) 并无法自行解决问题 I have read the [documentation](https://github.com/ZhuYanzhen1/miniFOC/wiki) and was unable to solve the issue.

### Description

`foc_calculate_dutycycle()`这个函数计算的是FOC三相电压的输出，但是计算方法看着并非是SVPWM而是SinePWM。
在SimpleFOC给的描述中SinePWM的计算方法包括Inverse Park transformation和Inverse Clarke transformation，计算方式如下:
- Inverse Park transformation

$$U_{\alpha}=U_d*cos(\theta)-U_q*sin(\theta)$$

$$U_{\beta}=U_d*sin(\theta)+U_q*sin(\theta)$$

一般只需要切向的$U_q$而不需要径向的$U_d$，故而$U_d=0$是期望值。
- Inverse Clarke transformation

$$u_a=U_{\alpha}$$

$$u_b=\frac{-U_{\alpha}+\sqrt{3}U_{\beta}}{2}$$

$$u_b=\frac{-U_{\alpha}-\sqrt{3}U_{\beta}}{2}$$

在作者的设计代码中是这样处理的：
```c
void foc_calculate_dutycycle(float elect_angle, float d, float q, float *u, float *v, float *w) {
    float alpha, beta;

    /* fast calculation of cosine and sine value of electric angle */
    float cf = fast_cos(elect_angle);
    float sf = fast_sin(elect_angle);

    /* firstly, the inverse Park transform is calculated */
    alpha = d * cf - q * sf;
    beta = q * cf + d * sf;

    /* secondly, the inverse Clarke transform is calculated */
    *u = 0.5f - alpha / VBUS;
    *v = 0.5f + (alpha * 0.5f - beta * 0.866025404f) / VBUS;
    *w = 1.5f - *u - *v;
}
```
`0.5`以及`0.15`这样奇怪的常量设置能否解释一下具体原因，以及整体计算方式应当归为SinePWM调制而不是SVPWM，与您的工程描述相悖。
@

### Possible Solution

_No response_

ZhuYanzhen1, 2022-08-01:
感谢您提出上述问题。在初期开发版本[2d309e904e5c3ea1071f60b64bcca6f0a0b3b80f](https://github.com/ZhuYanzhen1/miniFOC/commit/2d309e904e5c3ea1071f60b64bcca6f0a0b3b80f)中使用的是SVPWM，后续忘记更改回来了。现在仓库中已经更新该调制方法，并可以通过宏进行切换。值`0.5`和`1.5`是由于PWM产生方式被设置为了中央对齐，所以需要提供一个中间占空比的偏置使得负值能够被接受。

HangX-Ma, 2022-08-01:
感谢您的及时回复与更正解答，期待更多的学习与技术探讨。

Closed 2022-08-01.

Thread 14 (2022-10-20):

[Bug]

liaozhelin, 2022-10-20:
### Verify steps

- [X] 如果你可以自己 debug 并解决的话，提交 PR 吧。 <br>Is this something you can **debug and fix**? Send a pull request! Bug fixes and documentation fixes are welcome.
- [X] 我已经在 [Issue Tracker](……/) 中找过我要提出的问题。<br>I have searched on the [issue tracker](……/) for a related issue.
- [X] 我已经仔细看过 [Documentation](https://github.com/ZhuYanzhen1/miniFOC/wiki) 并无法自行解决问题。 <br>I have read the [documentation](https://github.com/ZhuYanzhen1/miniFOC/wiki) and was unable to solve the issue.
- [X] 这是 miniFOC 核心的问题，并非我所使用的 miniFOC 衍生版本的特定问题。  <br>This is an issue of the miniFOC core, not to the derivatives of miniFOC.

### miniFOC version

v1.1.2

### What OS are you seeing the problem on?

_No response_

### miniFOC config

```yaml
/**************************************************************************//**
  \file     config.h
  \brief    used to place important parameter configurations for users
  \author   Lao·Zhu
  \version  V1.0.3
  \date     1. August 2023
 ******************************************************************************/

#ifndef MINIFOC__CONFIG_H_
#define MINIFOC__CONFIG_H_

/*! \brief bus voltage is 8.0V */
#define VBUS            8.0f
/*! \brief set BLDC polar pairs to 7 */
#define POLAR_PAIRS     7
/*! \brief SC60228 resolution is 2^8 = 4096 */
#define ENCODER_RESO    4096
/*! \brief set calibrate torque to 0.5 */
#define CALI_TORQUE     0.5f
/*! \brief Not using space vector pulse width modulator */
#define USE_SVPWM       1

/*! \brief set UART baud rate to 512000 */
#define UART_BAUDRATE   115200
/*! \brief set PWM frequency to 20kHz */
#define PWM_FREQUENCY   20
/*! \brief set FOC loop frequency to 8kHz */
#define TIM2_FREQUENCY  8
/*! \brief set speed/angle PID loop frequency to 100Hz */
#define TIM13_FREQUENCY 100
/*! \brief set speed update frequency to 200Hz */
#define SPEED_UP_FREQ   200
/*! \brief set SPI frequency to 72 / 16 = 4.5MHz */
#define SPI_PRESCALE    SPI_PSC_16

/*! \brief UART preemption priority set to 1 */
#define UART_PRIORITY   1
/*! \brief TIMER2 preemption priority set to 2 */
#define TIM2_PRIORITY   2
/*! \brief TIMER13 preemption priority set to 3 */
#define TIM13_PRIORITY  3

/*! \brief User flash space start address, 1KB user flash */
#define FMC_WRITE_START_ADDR    0x08007C00UL

#endif //MINIFOC__CONFIG_H_
```

### miniFOC log

```shell
正常
```

### Description

首先感谢大佬，提供了一个这么完善的项目，收获颇多
下面是我根据您的资料复刻的minifoc，我自己修改了芯片为GD32f130C6T6(QFN的涨价了些)：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

主要遇到下面这些问题，因为本人无法解决，所以来麻烦大佬看看，十分感谢！

1. 手动在main函数中加入foc计算以及输出控制，电机可以旋转，但是使用原代码烧录后，打开上位机，设定好波特率后，可以看到图表内有编码器数据，但是手动旋转电机360度会出现数据突然间跳很大的情况：

   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

2. 使用上位机中三种控制模式，点击Start后，调整下方滑块电机均无反应：

   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

再次感谢大佬！

DeepSkyViewer, 2022-10-20:
呃，你确定没发错吧，我什么时候提供过foc的资料呢

---Original---
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

ZhuYanzhen1, 2022-10-20:
@liaozhelin 手动旋转电机出现的值突然归零是因为旋转电机超过360度之后会自动回到零度，这属于正常现象。另外如果想要使用上位机进行调试，必须要用串口接收中断绑定mdtp回调函数并且在main函数中进行状态机切换，这一部分你可以参考我的源码。

liaozhelin, 2022-10-20:
> @liaozhelin 手动旋转电机出现的值突然归零是因为旋转电机超过360度之后会自动回到零度，这属于正常现象。另外如果想要使用上位机进行调试，必须要用串口接收中断绑定mdtp回调函数并且在main函数中进行状态机切换，这一部分你可以参考我的源码。

好的，感谢大佬😎
我刚才重新修改测试了一下，现在上位机角度模式可以动了，PID参数也可以调整。
后续仔细研究下您的源码学习下，十分感谢。

ZhuYanzhen1, 2022-10-21:
好的

Closed 2022-10-21.

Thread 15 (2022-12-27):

支持步进电机吗

Mountain03, 2022-12-27:
### Verify steps

- [X]  我已经在 [Issue Tracker](……/) 中找过我要提出的请求<br> I have searched on the [issue tracker](……/) for a related feature request.
- [X]  我已经仔细看过 [Documentation](https://github.com/ZhuYanzhen1/miniFOC/wiki) 并无法自行解决问题 I have read the [documentation](https://github.com/ZhuYanzhen1/miniFOC/wiki) and was unable to solve the issue.

### Description

步进电机支持吗,有方案吗

### Possible Solution

_No response_

ZhuYanzhen1, 2023-06-30:
目前还不支持，miniFOC是为BLDC开发的驱动方案。

Closed 2023-06-30.

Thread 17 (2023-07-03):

[Feature] 这么便宜的方案，不知道有没有成品？  另外，能扩展到多大功率？

wpq3142, 2023-07-03:
### Verify steps

- [X]  我已经在 [Issue Tracker](……/) 中找过我要提出的请求<br> I have searched on the [issue tracker](……/) for a related feature request.
- [X]  我已经仔细看过 [Documentation](https://github.com/ZhuYanzhen1/miniFOC/wiki) 并无法自行解决问题 I have read the [documentation](https://github.com/ZhuYanzhen1/miniFOC/wiki) and was unable to solve the issue.

### Description

这么便宜的方案，不知道有没有成品？  另外，能扩展到多大功率？

### Possible Solution

这么便宜的方案，不知道有没有成品？  另外，能扩展到多大功率？

ZhuYanzhen1, 2023-07-10:
没有成品出售，最高功率等级应该可以到数千瓦。

pandysong, 2024-09-02:
Let's crowd funding.

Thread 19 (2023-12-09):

催更Wiki😁

GitHub-yiming, 2023-12-09:
### Verify steps

- [X]  我已经在 [Issue Tracker](……/) 中找过我要提出的请求<br> I have searched on the [issue tracker](……/) for a related feature request.
- [X]  我已经仔细看过 [Documentation](https://github.com/ZhuYanzhen1/miniFOC/wiki) 并无法自行解决问题 I have read the [documentation](https://github.com/ZhuYanzhen1/miniFOC/wiki) and was unable to solve the issue.

### Description

催更Wiki😁

### Possible Solution

_No response_

ZhuYanzhen1, 2023-12-11:
最近忙一些论文还有期末考的事情没时间更新，预计寒假期间可以继续更新。

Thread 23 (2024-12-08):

[Feature] 请问上位机软件开源吗

junchao98, 2024-12-08:
### Verify steps

- [X]  我已经在 [Issue Tracker](……/) 中找过我要提出的请求<br> I have searched on the [issue tracker](……/) for a related feature request.
- [X]  我已经仔细看过 [Documentation](https://github.com/ZhuYanzhen1/miniFOC/wiki) 并无法自行解决问题 I have read the [documentation](https://github.com/ZhuYanzhen1/miniFOC/wiki) and was unable to solve the issue.

### Description

请问下在上位机软件（monitor_win10_x86_64）中修改pid参数时，参数是否会实时生效
高分辨率屏幕下，软件UI有点错乱，想改改但似乎目前没有开源

### Possible Solution

_No response_

Closed 2024-12-12.

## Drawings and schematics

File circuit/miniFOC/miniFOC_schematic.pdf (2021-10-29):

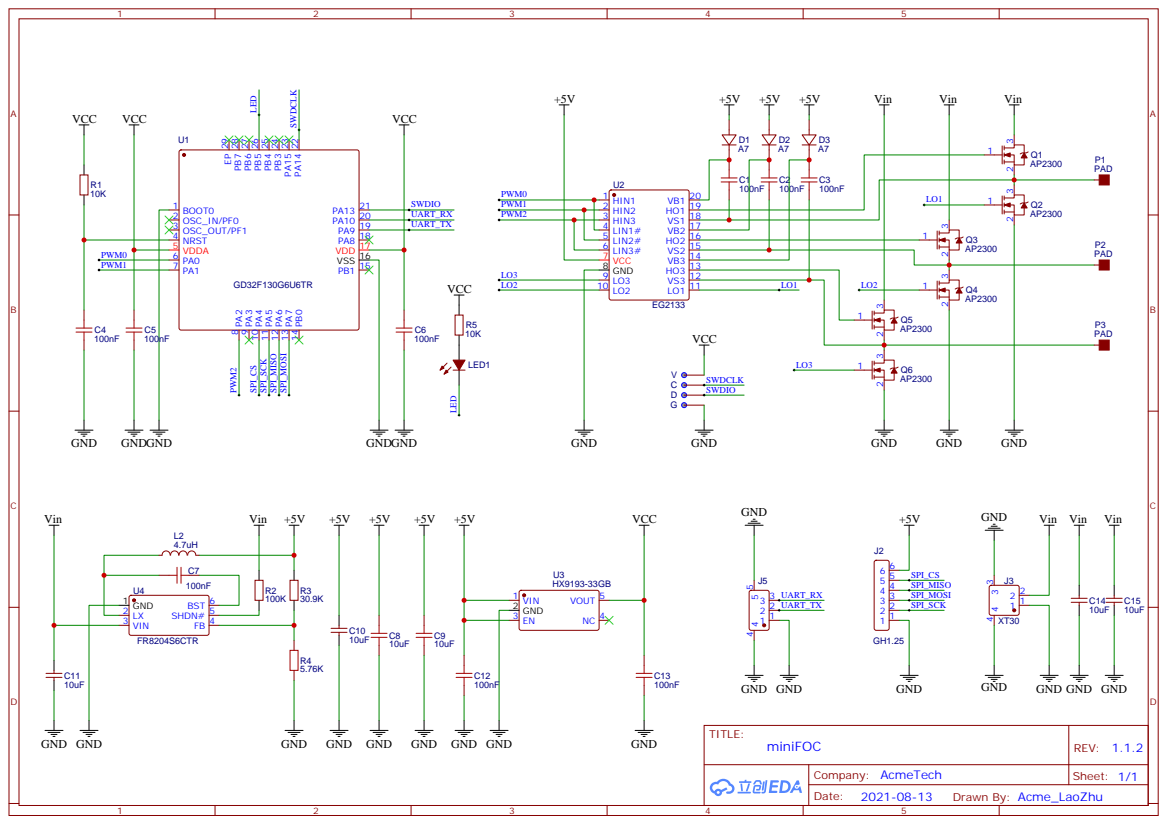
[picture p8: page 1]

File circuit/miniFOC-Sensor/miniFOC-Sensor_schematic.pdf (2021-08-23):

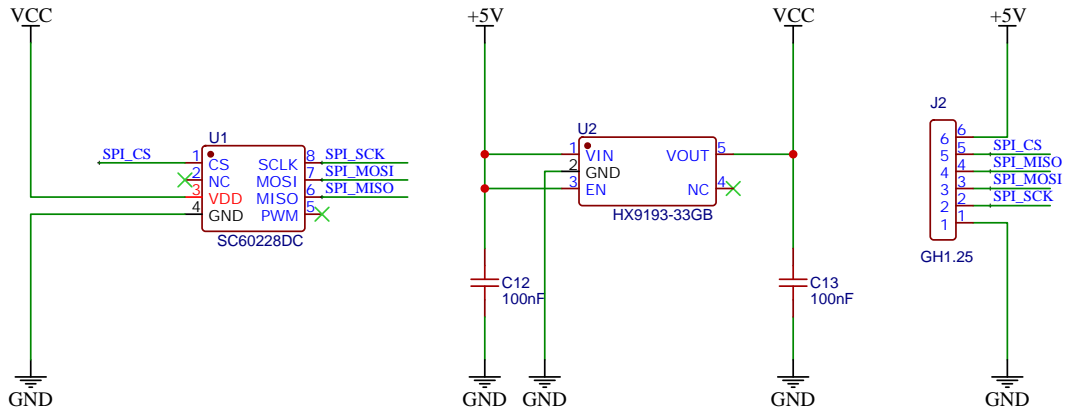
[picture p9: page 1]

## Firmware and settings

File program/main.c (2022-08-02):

/**************************************************************************//**
  \file     main.c
  \brief    miniFOC main source file, The relevant operations and main function
            after unpacking of medium capacity transmission protocol are implemented
            in this document.
  \author   Lao·Zhu
  \version  V1.0.2
  \date     29. October 2021
 ******************************************************************************/

#include "main.h"

/*!
    \brief used to indicate the current status of miniFOC
    \param
      1 calibrate motor phase and sensor offset  \n
      2 enable the motor                         \n
      3 disable the motor                        \n
      4 return current parameters
*/
static volatile unsigned char minifoc_fsm_state = 0;

/*!
    \brief     user callback function for unpacking completion of medium capacity transport protocol
    \param[in] pid: medium capacity transport protocol package id
    \param[in] data: received data array of size 8 bytes
*/
void mdtp_callback_handler(unsigned char pid, const unsigned char *data) {
    /* pack0 is the control pack of miniFOC */
    if (pid == 0) {
        unsigned int receive_int32;
        switch (data[0]) {
            case 0x0F:
                /* 0x0F is used to calibrate motor phase and sensor offset */
                minifoc_fsm_state = 1;
                break;

            case 0x1E:
                if (foc_parameter_available_flag == 1) {
                    /* 0x1E used to enable the motor */
                    minifoc_fsm_state = 2;

                    /* configure pid parameters for (torque/speed/angle) loop */
                    if (pid_parameter_available_flag == 1)
                        pid_config(data[1]);
                    else
                        pid_config(TORQUE_LOOP_CONTROL);
                }
                break;

            case 0x2D:
                /* 0x2D used to disable the motor */
                minifoc_fsm_state = 3;
                break;

            case 0x3C:
                /* 0x3C used to set user expect */
                receive_int32 = (data[4] << 24) | (data[5] << 16) | (data[6] << 8) | data[7];
                if (pid_parameter_available_flag == 1) {
                    switch (pid_control_mode_flag) {
                        default:
                        case TORQUE_LOOP_CONTROL:FOC_Struct.user_expect = int32_to_float(receive_int32);
                            break;
                        case SPEED_LOOP_CONTROL:speed_pid_handler.expect = int32_to_float(receive_int32);
                            break;
                        case ANGLE_LOOP_CONTROL:angle_pid_handler.expect = int32_to_float(receive_int32);
                            break;
                    }
                } else
                    FOC_Struct.user_expect = int32_to_float(receive_int32);
                break;

            case 0x4B:
                /* 0x4D used to set speed pid kp */
                receive_int32 = (data[4] << 24) | (data[5] << 16) | (data[6] << 8) | data[7];
                speed_pid_handler.kp = int32_to_float(receive_int32);
                break;

            case 0x5A:
                /* 0x5A used to set speed pid ki */
                receive_int32 = (data[4] << 24) | (data[5] << 16) | (data[6] << 8) | data[7];
                speed_pid_handler.ki = int32_to_float(receive_int32);
                break;

            case 0x69:
                /* 0x69 used to set speed pid kd */
                receive_int32 = (data[4] << 24) | (data[5] << 16) | (data[6] << 8) | data[7];
                speed_pid_handler.kd = int32_to_float(receive_int32);
                break;

            case 0x78:
                /* 0x78 used to set speed pid summary maximum */
                receive_int32 = (data[4] << 24) | (data[5] << 16) | (data[6] << 8) | data[7];
                speed_pid_handler.sum_maximum = int32_to_float(receive_int32);
                break;

            case 0x87:
                /* 0x87 used to set angle pid kp */
                receive_int32 = (data[4] << 24) | (data[5] << 16) | (data[6] << 8) | data[7];
                angle_pid_handler.kp = int32_to_float(receive_int32);
                break;

            case 0x96:
                /* 0x96 used to set angle pid ki */
                receive_int32 = (data[4] << 24) | (data[5] << 16) | (data[6] << 8) | data[7];
                angle_pid_handler.ki = int32_to_float(receive_int32);
                break;

            case 0xA5:
                /* 0xA5 used to set angle pid kd */
                receive_int32 = (data[4] << 24) | (data[5] << 16) | (data[6] << 8) | data[7];
                angle_pid_handler.kd = int32_to_float(receive_int32);
                break;

            case 0xB4:
                /* 0xB4 used to set angle pid summary maximum */
                receive_int32 = (data[4] << 24) | (data[5] << 16) | (data[6] << 8) | data[7];
                angle_pid_handler.sum_maximum = int32_to_float(receive_int32);
                break;

            case 0xC3:
                /* 0xC3 used to return current value */
                minifoc_fsm_state = 4;
                break;

            case 0xD2:
                /* 0xD2 used to write byte to flash */
                minifoc_fsm_state = 5;
                pid_parameter_available_flag = 1;
                break;
            default:break;
        }
    }
}

/*!
    \brief main function
*/
int main(void) {
    /* 4 bits for preemption priority 0 bits for subpriority */
    nvic_priority_group_set(NVIC_PRIGROUP_PRE4_SUB0);

    /* configure peripherals */
    led_config();
    uart_config();
    pwm_config();
    spi_config();

    /* configure filter and pid parameters for pid algorithm */
    filter_config();
    pid_config(TORQUE_LOOP_CONTROL);

    /* configure systick timer for delay_ms() function */
    systick_config();

    /* read all parameters from flash */
    flash_read_parameters();

    /* correct the mechanical angle zero deviation */
    encoder_zeroing();

    while (1) {
        switch (minifoc_fsm_state) {
            case 1:
                /* disable timer to stop foc calculate loop */
                timer2_disable();
                timer13_disable();

                /* automatic phase sequence detection and correction */
                foc_calibrate_phase();

                /* correct the mechanical angle zero deviation */
                encoder_zeroing();

                /* re-write the parameters to flash */
                flash_write_parameters();
                minifoc_fsm_state = 0;
                break;

            case 2:
                /* delay to wait for the motor to respond */
                delayms(1000);

                /* configure timer for foc calculate loop */
                timer2_config();
                if (pid_control_mode_flag != TORQUE_LOOP_CONTROL)
                    timer13_config();
                minifoc_fsm_state = 0;
                break;

            case 3:
                /* disable timer to stop foc calculate loop */
                timer2_disable();
                if (pid_control_mode_flag != TORQUE_LOOP_CONTROL)
                    timer13_disable();
                minifoc_fsm_state = 0;
                break;

            case 4:
                /* transmit current value to monitor */
                report_local_variable();
                minifoc_fsm_state = 0;
                break;

            case 5:
                /* disable timer to stop foc calculate loop */
                timer2_disable();
                timer13_disable();

                /* write data to flash */
                flash_write_parameters();
                minifoc_fsm_state = 0;
                break;

            case 0:
            default:
                /* transmit angle and speed to monitor */
                report_angle_speed();
                led_toggle();
                delayms(50);
                break;
        }
    }
}

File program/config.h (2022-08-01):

/**************************************************************************//**
  \file     config.h
  \brief    used to place important parameter configurations for users
  \author   Lao·Zhu
  \version  V1.0.3
  \date     1. August 2023
 ******************************************************************************/

#ifndef MINIFOC__CONFIG_H_
#define MINIFOC__CONFIG_H_

/*! \brief bus voltage is 8.0V */
#define VBUS            8.0f
/*! \brief set BLDC polar pairs to 7 */
#define POLAR_PAIRS     7
/*! \brief SC60228 resolution is 2^8 = 4096 */
#define ENCODER_RESO    4096
/*! \brief set calibrate torque to 0.5 */
#define CALI_TORQUE     0.5f
/*! \brief Not using space vector pulse width modulator */
#define USE_SVPWM       1

/*! \brief set UART baud rate to 512000 */
#define UART_BAUDRATE   512000
/*! \brief set PWM frequency to 20kHz */
#define PWM_FREQUENCY   20
/*! \brief set FOC loop frequency to 8kHz */
#define TIM2_FREQUENCY  8
/*! \brief set speed/angle PID loop frequency to 100Hz */
#define TIM13_FREQUENCY 100
/*! \brief set speed update frequency to 200Hz */
#define SPEED_UP_FREQ   200
/*! \brief set SPI frequency to 72 / 16 = 4.5MHz */
#define SPI_PRESCALE    SPI_PSC_16

/*! \brief UART preemption priority set to 1 */
#define UART_PRIORITY   1
/*! \brief TIMER2 preemption priority set to 2 */
#define TIM2_PRIORITY   2
/*! \brief TIMER13 preemption priority set to 3 */
#define TIM13_PRIORITY  3

/*! \brief User flash space start address, 1KB user flash */
#define FMC_WRITE_START_ADDR    0x08007C00UL

#endif //MINIFOC__CONFIG_H_

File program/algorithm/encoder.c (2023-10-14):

/**************************************************************************/ /**
   \file     encoder.c
   \brief    this file contains the code implementation of angle acquisition
             and initialization functions of sc60228 and sc60224.
   \author   Lao·Zhu
   \version  V1.0.2
   \date     29. October 2021
  ******************************************************************************/

#include "encoder.h"
#include "config.h"
#include "filter.h"
#include "foc.h"
#include "gd32f1x0.h"
#include "spi.h"
#include "system.h"
#include "timer.h"

/*!
    \brief mechanical angle offset, which is used to align the mechanical
           angle with the zero point of the electrical angle.
*/
volatile unsigned short machine_angle_offset = 0;
/*!
    \brief the mechanical angle at the last moment is used to calculate
           the angle differential value and realize the angle measurement
           function.
*/
volatile static unsigned short last_mechanical_angle = 0;
/*!
    \brief the total mechanical angle since power on is used to calculate
           the angle integral value and realize the angle measurement function.
*/
volatile static uint64_t total_machine_angle = UINT64_MAX / 2;
/*!
    \brief the mechanical angle at the last moment is used to calculate
           the rotation speed of the motor rotor.
*/
volatile static uint64_t systick_mechanical_angle_last = UINT64_MAX / 2;

/*!
    \brief delay function for magnetic encoder
*/
void encoder_delay(void) {
  /* use loop functions to delay time */
  unsigned char delay_counter = 0xff;
  while (delay_counter)
    delay_counter--;
}

/*!
    \brief     read data from the register of the magnetic encoder
    \param[in] TxData: data to be sent to magnetic encoder
    \retval    data read from magnetic encoder
*/
unsigned short encoder_read_data(unsigned short TxData) {
  unsigned short data;

  /* pull down the CS pin and prepare to send data */
  gpio_bit_write(GPIOA, GPIO_PIN_4, RESET);
  encoder_delay();

  /* call SPI related functions to send and receive data */
  data = spi_readwrite_halfworld(TxData);
  encoder_delay();

  /* pull up CS pin to end sending data */
  gpio_bit_write(GPIOA, GPIO_PIN_4, SET);
  return data;
}

/*!
    \brief  read mechanical angle directly from encoder
    \retval register raw data reading back
*/
unsigned short encoder_get_mechanical_angle(void) {
  /* read back register raw data */
  unsigned short angle = encoder_read_data(0x0000) >> 4;

  /* statistical total rotation angle */
  total_machine_angle = total_machine_angle + angle - last_mechanical_angle;
  last_mechanical_angle = angle;

  /* returns the result of subtracting the offset. */
  return ((total_machine_angle - machine_angle_offset) % ENCODER_RESO);
}

/*!
    \brief  according to the electrical angle calculated from the mechanical
   angle, this function will call encoder_get_mechanical_angle() function.
    \retval register raw data reading back
*/
float encoder_get_electronic_angle(void) {
  /* read back the mechanical angle directly from the magnetic encoder */
  unsigned short tmp_mechanical_angle = encoder_get_mechanical_angle();

  /* calculate and update the mechanical angle and electric angle */
  FOC_Struct.mechanical_angle =
      (float)tmp_mechanical_angle * MECHANGLE_COEFFICIENT;
  float electric_angle =
      (float)(tmp_mechanical_angle % (ENCODER_RESO / POLAR_PAIRS)) *
      ELECANGLE_COEFFICIENT;
  return electric_angle;
}

/*!
    \brief called every 2 milliseconds to calculate the speed.
*/
void encoder_update_speed(void) {
  /* calculate the difference between this angle and the last angle */
  short tmp_mechanical_angle_velocity =
      (short)(total_machine_angle - systick_mechanical_angle_last);

  /* send it to low-pass filter for filtering to prevent PID high-frequency
   * oscillation */
  FOC_Struct.rotate_speed = filter_update_value(
      (Filter_Structure_t *)&velocity_filter, tmp_mechanical_angle_velocity);
  systick_mechanical_angle_last = total_machine_angle;
}

/*!
    \brief correct the mechanical angle zero deviation between the magnetic
   encoder and FOC.
*/
void encoder_zeroing(void) {
  float u, v, w;
  /* delay to wait for the power supply voltage to be normal */
  delayms(1000);

  /* set that there is only a magnetic field on the straight axis. */
  foc_calculate_dutycycle(0, CALI_TORQUE, 0, &u, &v, &w);
  update_pwm_dutycycle(u, v, w);
  delayms(300);
  machine_angle_offset = 0;
  total_machine_angle = UINT64_MAX / 2;

  /* read the angle at this time as the offset angle */
  machine_angle_offset = encoder_read_data(0x0000) >> 4;

  /* zero the torque in all directions to release the motor */
  foc_calculate_dutycycle(0, 0, 0, &u, &v, &w);
  update_pwm_dutycycle(u, v, w);
  delayms(300);
}

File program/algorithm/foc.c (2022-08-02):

/**************************************************************************//**
  \file     foc.c
  \brief    this document is mainly the code implementation of motor
            phase sequence correction and FOC algorithm.
  \author   Lao·Zhu
  \version  V1.0.3
  \date     1. August 2023
 ******************************************************************************/

#include "foc.h"
#include "config.h"
#include "fast_math.h"
#include "encoder.h"
#include "system.h"
#include "timer.h"

/*!
    \brief FOC handler
*/
volatile FOC_Structure_t FOC_Struct;
/*!
    \brief motor phase sequence flag variable
*/
volatile unsigned char phase_sequence = 0;
/*!
    \brief flag variable for FOC parameter availability
*/
unsigned char foc_parameter_available_flag = 1;

/*!
    \brief automatic phase sequence detection and correction
*/
void foc_calibrate_phase(void) {
    unsigned short last_angle = 0, positive_counter = 0;
    float u, v, w, angle = 0;

    /* set that there is only a magnetic field on the straight axis */
    foc_calculate_dutycycle(0, CALI_TORQUE, 0, &u, &v, &w);
    update_pwm_dutycycle(u, v, w);
    delayms(1000);

    for (unsigned char counter = 0; counter < 50; ++counter) {
        /* measure current motor angle */
        unsigned short current_angle = encoder_get_mechanical_angle();

        /* judge whether the current angle increases */
        if (current_angle > last_angle)
            positive_counter++;

        /* update last angle as current angle */
        last_angle = current_angle;

        /* set that there is only a magnetic field on the straight axis */
        foc_calculate_dutycycle(angle, CALI_TORQUE, 0, &u, &v, &w);
        angle += 0.2f;
        update_pwm_dutycycle(u, v, w);
        delayms(20);
    }
    for (unsigned char counter = 0; counter < 50; ++counter) {
        /* measure current motor angle */
        unsigned short current_angle = encoder_get_mechanical_angle();

        /* judge whether the current angle decreases */
        if (current_angle < last_angle)
            positive_counter++;

        /* update last angle as current angle */
        last_angle = current_angle;

        /* set that there is only a magnetic field on the straight axis */
        foc_calculate_dutycycle(angle, CALI_TORQUE, 0, &u, &v, &w);
        angle -= 0.2f;
        update_pwm_dutycycle(u, v, w);
        delayms(20);
    }

    /* zero the torque in all directions to release the motor */
    foc_calculate_dutycycle(0, 0, 0, &u, &v, &w);
    update_pwm_dutycycle(u, v, w);
    delayms(300);

    if (positive_counter >= 75)
        phase_sequence = 0;
    else if (positive_counter < 25)
        phase_sequence = 1;
    else
        while (1);
}

/*!
    \brief      calculate the corresponding three-phase PWM duty cycle under the current electrical angle
    \param[in]  elect_angle: electrical angle of motor rotor, in radian system
    \param[in]  d: expected field strength in the direct axis direction of the motor
    \param[in]  q: expected field strength in the quadrature axis direction of the motor
    \param[out] u: calculation results of U-phase duty cycle
    \param[out] v: calculation results of V-phase duty cycle
    \param[out] w: calculation results of W-phase duty cycle
*/
void foc_calculate_dutycycle(float elect_angle, float d, float q, float *u, float *v, float *w) {
    float alpha, beta;

    /* fast calculation of cosine and sine value of electric angle */
    float cf = fast_cos(elect_angle);
    float sf = fast_sin(elect_angle);

#if USE_SVPWM == 0
    /* firstly, the inverse Park transform is calculated */
    alpha = d * cf - q * sf;
    beta = q * cf + d * sf;

    /* secondly, the inverse Clarke transform is calculated */
    *u = 0.5f - alpha / VBUS;
    *v = 0.5f + (alpha * 0.5f - beta * 0.866025404f) / VBUS;
    *w = 1.5f - *u - *v;
#else
    float tmp2, tmp3, Ta, Tb, Tc;
    char vec_sector = 3;

    /* firstly, the inverse Clarke transform is calculated */
    alpha = d * cf - q * sf;
    beta = q * cf + d * sf;
    tmp2 = beta * 0.5f + alpha * 0.8660254f;
    tmp3 = tmp2 - beta;

    /* judge which sector the magnetic vector is in at this time */
    vec_sector = ((*(unsigned int *) &tmp2) >> 31) ? vec_sector : (vec_sector - 1);
    vec_sector = ((*(unsigned int *) &tmp3) >> 31) ? vec_sector : (vec_sector - 1);
    vec_sector = ((*(unsigned int *) &beta) >> 31) ? (7 - vec_sector) : vec_sector;

    /* the proportion of each phase is calculated by six sector modulation method */
    switch (vec_sector) {
        case 1:
        case 4: Ta = tmp2;
            Tb = beta - tmp3;
            Tc = -tmp2;
            break;
        case 2:
        case 5:Ta = tmp3 + tmp2;
            Tb = beta;
            Tc = -beta;
            break;
        default:Ta = tmp3;
            Tb = -tmp3;
            Tc = -(beta + tmp2);
            break;
    }

    /* calculate the duty cycle in center alignment mode */
    *u = (Ta / VBUS) * 0.5f + 0.5f;
    *v = (Tb / VBUS) * 0.5f + 0.5f;
    *w = (Tc / VBUS) * 0.5f + 0.5f;
#endif
}

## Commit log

2021-08-14 add bill of material for circuit
    [BOM_miniFOC.csv, BOM_miniFOC.xlsx]
2021-08-14 add schematic of lceda for circuit and add schematic image
2021-08-14 renew bom for circuit
    [BOM_miniFOC.csv, BOM_miniFOC.xlsx]
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2021-08-14 add pick and place file and gerber files for circuit
    [Gerber_BoardOutline.GKO, Gerber_BottomLayer.GBL, Gerber_BottomPasteMaskLayer.GBP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]
2021-08-17 Modified system files in program
    [board.cfg]
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2021-08-17 fix stage bugs for ci
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2021-08-18 renew miniFOC PCB files and manufacture files
    [BOM_miniFOC.csv, BOM_miniFOC.xlsx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]
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2021-08-23 Add miniFOC Sensor manufacture files to manufacture dir
    [BOM_miniFOC-Sensor.csv, BOM_miniFOC-Sensor.xlsx, BOM_miniFOC.csv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]
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2021-08-24 Add UART0 initialization code, file author declaration, function declaration and code comments. Add config header file to facilitate users to modify important parameters.
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2021-08-25 Add priority initialization code, add UART priority configuration macro, and delete redundant library files.
2021-08-25 Some data receiving functions are realized. Annotate the functions in the system file. Fixed missing systick handler. The memset function is rewritten, and the program volume can be reduced without u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
    [gd32f1x0_it.c, uart.c]
2021-08-25 Complete the unpacking program of finite state machine for medium capacity data transmission protocol.
2021-08-26 Add the packet function of medium capacity transmission protocol. When the data packet is received, it is sent back according to the original packet to test whether the function of receiving and send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
2021-08-26 Add the processing of medium capacity transmission protocol if all data byte is 0xff. Add comments for the new function.
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2021-08-28 Add and update PWM duty cycle function. Add comments for PWM initialization function and modify initialization channel.
2021-08-31 Fixed the problem that the millisecond delay function could not be used
    [board.cfg]
2021-09-02 Add read and initialization functions of magnetic encoder. Add comments for SPI related functions and move SPI frequency division coefficient to config file for configuration.
2021-09-02 Adjust PWM to 10kHz to prevent MOSFET from heating and serious burning. The PWM frequency calculation function is modified.
    [config.h, timer.c]
2021-09-03 The problem of reading angle failure of magnetic encoder is solved. Modified stack space allocation. Added float and int16 type conversion functions.
    [config.h, encoder.c, main.c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]
2021-09-03 The electric angle correction program is added. The pole number and encoder resolution are added to the config file for modification. Corrected PWM initialization duty cycle to prevent power on burn 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
    [config.h, encoder.c, main.c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]
2021-09-03 Add comments for the magnetic encoder function. Add notes for SPI data transceiver function. Add comments for float and int16 conversion functions. Modify the location and name of the linked file.
2021-09-03 Update the PCB and manufacturing files of the sensor board, and fix the problem of interface image.
    [Gerber_BoardOutline.GKO, Gerber_BottomLayer.GBL, Gerber_BottomPasteMaskLayer.GBP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]
2021-09-05 Fix the important error of magnetic encoder reading program, namely SPI timing problem. The initialization program of magnetic encoder is deleted, and initialization is not required.
    [config.h, encoder.c, main.c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]
2021-09-05 Fixed the logic problem of serial port receiving unpacking program. The FOC closed-loop frequency is modified to 8kHz. Extended waiting time for startup. Change global variables to static variables.
    [config.h, encoder.c, foc.c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]
2021-09-05 Add comments for the interrupt service function. Add speed calculation function.
2021-09-05 The speed calculation code and sliding window filter function are added to make the speed smoother.
2021-09-06 Added phase sequence correction code, which has been verified to be available.
    [foc.c]
2021-09-07 Modify the motor phase sequence correction algorithm, speed up the correction process and add protection measures.
    [foc.c, gd32f1x0_it.c, main.c]
2021-09-07 Fix mdtp_callback_handler function name mismatch.
    [main.c, uart.c]
2021-09-08 The six sector modulation method for generating SVPWM is replaced by inverse Park transform.
    [foc.c]
2021-09-09 The program of saving correction parameters in flash is realized. The correction and start rotation are controlled through the serial port.
    [config.h, encoder.c, foc.c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]
2021-09-09 The unpacking program of medium capacity data transfer protocol was successfully transplanted to monitor tool.
2021-09-10 Add "calibrate" and "start / stop" control buttons and realize their functions.
2021-09-10 Add PID control algorithm and initialize the PID structure of speed loop and angle loop.
2021-09-10 Add comments to the reporting segment. Add PID initialization function. Add motor stop command.
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2021-09-11 Add timer disable code, which has not been tested.
2021-09-11 Adding different closed-loop codes has not been tested. Add program segments and commands to stop the motor.
2021-09-11 Fix the problem that the program section of stopping the motor does not jump out. Put the default mode into the config file for configuration.
    [config.h, main.c, timer.c]
2021-09-11 Realize the function of sending stop command by pressing the stop button.
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2021-09-12 Modify the control package ID in the monitor tool and realize the selection and switching of torque, speed and angle control modes.
2021-09-12 The function of torque control through slider is realized in monitor tool.
2021-09-12 Fixed the problem that the reverse speed could not be measured during speed calculation.
    [encoder.c]
2021-09-12 The circuit of minifoc is modified to separate the debug interface from the UART interface.
2021-09-13 The PCB circuit of minifoc is modified
    [BOM_miniFOC.csv, BOM_miniFOC.xlsx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]
2021-09-14 Add speed loop PID parameter configuration command. Modify the program that the user expects under the control of different loops.
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2021-09-16 Modify window average filter to one order low pass rc filter.
2021-09-18 Add speed loop PID debugging control for monitor.
2021-09-18 Add angle loop PID debugging control for monitor. And increase the maximum integral value to set the slider.
2021-09-20 Add the callback function for the change of speed loop PID parameter adjustment slider value, and modify the packet sending function to send different Zhi according to the change of different sliders
2021-09-20 Add the callback function for the change of angle loop PID parameter adjustment slider value. Add a few comments to the monitor code.
2021-09-20 Correct the FOC twice coordinate transformation annotation.
    [foc.c]
2021-09-21 A limiting function is added to the low-pass filter.
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2021-09-22 The validity judgment of PID parameters is added to prevent incorrect PID parameters from being used when PID parameters are not configured.
    [config.h, main.c]
2021-09-26 Change the judgment of the monitor after receiving the packet into a switch statement.
2021-09-26 Add the slider position and the maximum and minimum value change code for the monitor. Now the parameters of the motor can be parsed and reflected on the slider.
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2021-10-04 Correct the medium capacity data transfer protocol link in README.
2021-10-09 Doxygen configuration file is added, which can generate documents directly through the configuration file.
    [Doxygen.cfg]
2021-10-09 Modify the main page of Doxygen generated documents to readme file as the main page.
    [Doxygen.cfg]
2021-10-29 Modify the page content of GitHub page so that GitHub page is mainly used to display Doxygen documents.
    [Doxygen.cfg]
2021-10-29 Generate the Doxygen document and add it to the docs folder so that it can be displayed in the GitHub page.
    [Doxygen.cfg]
2021-10-29 The circuit is updated to solve the problem of burnout when the input voltage exceeds the Vgs voltage.
2021-11-04 It solves the problem of jamming after burning the new IC.
    [foc.c, main.c]
2021-11-04 Added the button and method of flash writing content control. There are still problems with parameter reading and slider display that need to be modified.
    [main.c]
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2022-08-02 Update Doxygen documentation
    [Doxygen.cfg]
2023-08-11 Fix bugs in total_machine_angle calculate and pid integer anti-constrain method.
    [encoder.c]
2023-10-14 Fixed some bugs in encoder mechanical angle calculation and deleted useless files.
    [encoder.c]

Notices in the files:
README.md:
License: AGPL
